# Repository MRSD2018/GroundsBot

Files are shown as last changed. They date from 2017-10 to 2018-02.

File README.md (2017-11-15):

# GroundsBot
A ~~flexible~~ system that can perform regular outdoor grounds maintenance tasks such a ~~sidewalk sweeping~~,
~~snow clearing~~ or grass cutting on extreme terrain for use by grounds care ~~and snow removal~~ companies.

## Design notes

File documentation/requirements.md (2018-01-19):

System Level Requirements

Mandatory Performance Requirements
ID,Requirement,Description

M.P.1, First time user inputs map within 15 minutes, GroundsBot should be easy to use  

M.P.2, System returns proposed route/coverage map within 5 minutes, related to M.P.1 GroundsBot should start up quickly to ease the mind of the user   

M.P.3, Cover 1/4 acre per hour on flat, unobstructed terrain, minimum coverage rate in ideal conditions

M.P.4, Cut 95% of the grass on flat, unobstructed terrain, minimum total coverage in ideal conditions

M.P.5, Navigate 30 degree sloped grass, GroundsBot should be able to handle steep slopes safely

M.P.6 , Detect 80% of static objects greater than 3 inches in height and 2 inches in width, GroundsBot should be able to recognize static obstacles in order to prevent collisions and mowing accidents 

M.P.7 , Detect 80% of dynamic objects greater than 6 inches in height and 6 inches in width travelling less than 4 mph, GroundsBot should be able to recognize obstacles in order to prevent collisions and mowing accidents 

M.P.8 , Mow to within 1 foot of detected obstacles , GroundsBot should be able to detect an obstacle (M.P.6) and navigate around it to continue its mowing path 

M.P.9 , Return home to within 5 feet of starting position , GroundsBot should return to its starting position to remove as much hassle from the user as possible   	  

Desirable Performance Requirements

ID,Requirement,Description

D.P.1 , Mow to within 3 inches of a detected obstacles , A stretch goal for when M.P.8 (mow within 1 ft. of obstacles) is achieved 

D.P.2 , Visually report mowing coverage and obstacles encountered , GroundsBot should report areas it missed to the user so the user knows where to manually mow to achieve full coverage

D.P.3 , Deck adjustable 0.5” to 2” , GroundsBot should be able to meet the grass height standards of different golf courses

Mandatory Non-Functional Requirements
ID,Requirement,Description

M.N.1 , Have a functional and easily accessible emergency stop , GroundsBot should be safe to use and easy to shut down in case of emergency

M.N.2 , Be clearly visible , GroundsBot should indicate its presence and status to everyone nearby 

M.N.3 , Do not tear up grass , GroundsBot should not ruin any area it travels over 

Desirable Non-Functional Requirements

ID,Requirement,Description
D.N.1 , Operates in low light conditions , GroundsBot should operate in low light conditions to avoid interrupting golfers

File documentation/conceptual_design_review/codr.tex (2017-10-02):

\documentclass[12pt]{extarticle}
\usepackage[utf8]{inputenc}
\usepackage{graphicx}
\usepackage{float}
\usepackage{array}
\usepackage{makecell} %line breaks inside table cells
\usepackage{changepage} %temp adjust margins
\usepackage[table]{xcolor} %color tables
\usepackage{outlines}
\usepackage{setspace}
\usepackage{multirow}
\usepackage[export]{adjustbox}% http://ctan.org/pkg/adjustbox
\usepackage{caption}
\usepackage{etoolbox}
\usepackage[margin=1in]{geometry}
\usepackage{tabularx}
\usepackage{titling}
\usepackage{titlesec}
\usepackage{helvet}
\usepackage{indentfirst}
\usepackage{arydshln} %dashed lines (must load in last)

\BeforeBeginEnvironment{tabular}{\fontsize{10}{12}\selectfont}
\AfterEndEnvironment{tabular}{}
\BeforeBeginEnvironment{tabularx}{\fontsize{10}{12}\selectfont}
\AfterEndEnvironment{tabularx}{}

\graphicspath{ {img/} }

\titleformat*{\section}{\bfseries\sffamily\fontsize{14}{16}\selectfont}
\titleformat*{\subsection}{\bfseries\sffamily\fontsize{12}{14}\selectfont}
\titleformat*{\subsubsection}{\bfseries\sffamily\fontsize{12}{14}\selectfont}

\captionsetup[table]{font={small, bf}}
\captionsetup[figure]{font={small, bf}}

\renewcommand{\baselinestretch}{1.1} 

\begin{document}

\definecolor{highlight}{HTML}{9DE6AA} %grudsbo green, light edition
\definecolor{maroon}{cmyk}{0,0.87,0.68,0.32}
\definecolor{badhighlight}{HTML}{FF0000}

\title{GroundsBot: Autonomous Golf Course Maintenance \\[.5ex]
		\Large Conceptual Design Review}
\date{September 2017}
\author{CMU MRSD Team A        \\ Sponsor: Discovery Robotics \\ David Evans \\
        Adam Driscoll \\ Henry Chen  \\
        Josh Bennett  \\ Joe Phaneuf \\ }

\maketitle
\def\svgwidth{\columnwidth}
\input{img/groundsbot_logo.pdf_tex}
\newpage

\begin{spacing}{0.95}
\tableofcontents
\end{spacing}

\newpage

\newpage
\section{Project Description}

People spend a lot of time mowing grass. This is particularly true for golf courses. Golf courses have hundreds of acres of land requiring careful maintenance. The median club in the United States spends \$1.2 million per year on maintenance \cite{clubbenchmarking}. A Pittsburgh area golf course superintendent \cite{interview-duxbury} revealed that his staff spends 65\% of their time mowing, and 60\% of that time is spent just on the rough. This is an industry ripe for automation.
\\

Autonomous mowers are commercially available today, however most of these units require buried wires, beacons, or extensive mapping to provide boundaries. For a golf course, the mowing area is so large that those setup methods are a barrier to deployment. The GroundsBot team aims to deliver an autonomous mower that can be deployed with minimal infrastructure, using a coarse boundary map provided by the user.

\newpage
\section{Use Case}
\begin{table}[H]
  \def\arraystretch{4}
   \setlength\tabcolsep{8pt}

\begin{tabularx}{\textwidth}{cX}
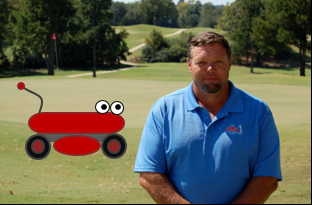
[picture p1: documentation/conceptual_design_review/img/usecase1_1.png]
 & 
Meet Steve. He's a golf course superintendent responsible for keeping the golf course looking professional. Right now, Steve and his groundskeeping team spend 65\% of their time just mowing grass. To save time, Steve just bought a GroundsBot unit to autonomously mow the rough around his golf course. \\
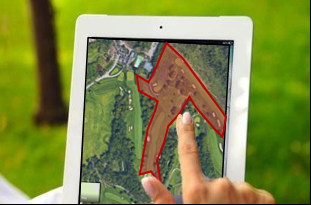
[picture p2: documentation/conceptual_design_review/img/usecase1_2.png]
 &
To start the mowing process, Steve first has to draw an outline of the area he wants mowed. He also highlights any zones Groundsbot should avoid while mowing.
\\
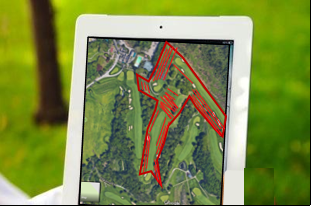
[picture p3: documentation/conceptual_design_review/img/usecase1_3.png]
 &
With the area to mow now outlined, the Groundsbot planning software creates a global route to cover all of the requested area. It avoids large obstacles like fairways, forests, and parking lots.
\\
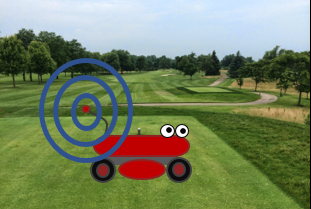
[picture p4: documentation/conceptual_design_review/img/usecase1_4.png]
 &
GroundsBot recieves the global route and localizes through GPS to determine where it is on the golf course.
\\
\end{tabularx}
\end{table}

\begin{table}[H]
   \def\arraystretch{4}
   \setlength\tabcolsep{8pt}

\begin{tabularx}{\textwidth}{cX}
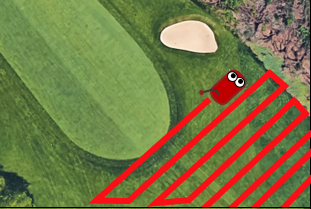
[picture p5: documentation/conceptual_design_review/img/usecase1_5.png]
 &
With the unit located and a global plan uploaded, GroundsBot begins mowing the area specified by Steve. It moves back and forth cutting the grass precisely, matching the quality care provided by Steve and his groundskeeping team.
\\
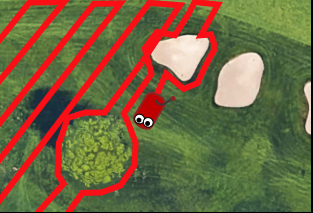
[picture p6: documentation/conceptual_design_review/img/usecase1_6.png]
 &
If GroundsBot encounters unplanned obstacles like sand traps or individual trees, GroundsBot avoids the obstacle and cuts around it. Once GroundsBot has avoided the obstacle in its path, it continues with the original plan.
\\
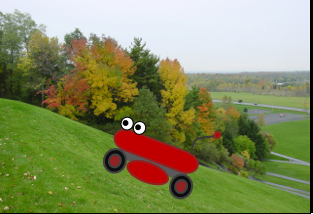
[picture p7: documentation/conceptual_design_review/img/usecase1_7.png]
 &
In order to maximize coverage, GroundsBot will navigate difficult terrain on a golf course, cutting the rough on steep hills.
\\
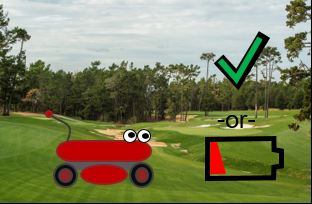
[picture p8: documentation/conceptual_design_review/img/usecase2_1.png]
 &
Once GroundsBot is finished or low on power, it notifies Steve and returns back to the charging dock.
\\

\end{tabularx}
\end{table}

\begin{table}[H]
   \def\arraystretch{4}
   \setlength\tabcolsep{8pt}

\begin{tabularx}{\textwidth}{cX}
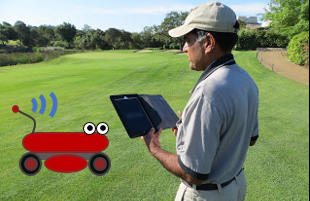
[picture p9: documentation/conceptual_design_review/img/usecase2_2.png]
 &
GroundsBot collected a lot of data while it was out cutting. It transfers diagnostics, coverage reports, and cutting data to Steve’s mobile device.
\\
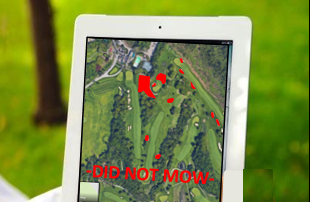
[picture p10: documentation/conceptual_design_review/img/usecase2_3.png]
 &
From here, Steve can analyze what areas of the course GroundsBot missed and what areas he has to send his team out to trim or tidy up.
\\
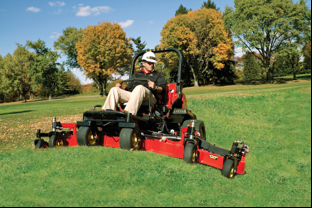
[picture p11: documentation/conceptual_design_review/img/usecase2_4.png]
 &
Steve sends out his groundskeeping team to quickly address missed spots or edging. This is a much faster experience for the team because they only have to touch up a few areas on the course.
\\
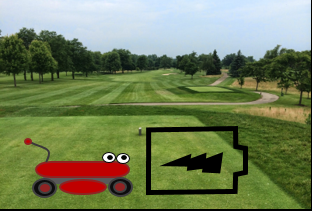
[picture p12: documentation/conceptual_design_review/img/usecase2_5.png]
 &
With the course looking professional, Steve and his groundskeeping team are happy they don’t have to worry about mowing. GroundsBot recharges to prepare for another day of mowing.
\\

\end{tabularx}
\end{table}

\newpage
\section{System Level Requirements}

The system requirements were decided upon to demonstrate a proof of concept autonomous lawn mower that can be set up with minimal added infrastructure. The only added infrastructure will be a docking station for GroundsBot. To accomplish this, GroundsBot must be able to localize with extreme accuracy in an unknown environment. GroundsBot must also be able to navigate consistently along a mowing path plan. Finally, GroundsBot must be able to detect and avoid any obstacles along the way.

\subsection{Mandatory Requirements}
\begin{center}
  \begin{table}[H]
  \caption{Mandatory Performance Requirements}
  \label{table:mandatory performance}

  \def\arraystretch{1.5}
  	\begin{tabularx}{\textwidth}{ lXX }
  	  \hline

		\sffamily\normalsize{ID} & \sffamily\normalsize{Requirement} & \sffamily\normalsize{Description} \\
    	M.P.1 &
    	First time user inputs map within 15 minutes &
    	GroundsBot should be easy to use \\
   		M.P.2 &
   		System returns proposed route/coverage map within 5 minutes &
   		Related to M.P.1, GroundsBot should start up quickly to ease the mind of the user \\
   		M.P.3 &
   		Cut 0-25\% overlap for 95\% of grass &
   		When mowing, GroundsBot should cut in a way that accomplishes full grass coverage while maintaining efficiency by reducing overlap\\
		M.P.4 &
		Mow 50$ft^2$ of 30 degree sloped grass &
		GroundsBot should be able to handle steep slopes to eliminate safety hazards \\
		M.P.5 &
		Detect 80\% of objects greater than 27 cubic inches &
		GroundsBot should be able to recognize obstacles in order to prevent collisions and mowing accidents \\
		M.P.6 &
		Mow to within 1 foot of detected obstacles &
		GroundsBot should be able to detect an obstacle (M.P.5) and navigate around it to continue its mowing path \\
		M.P.7 &
		Mow 90\% of a $\frac{1}{4}$ acre area &
		GroundsBot will encounter obstacles along the way preventing it from 100\% coverage \\
	\end{tabularx}
  \end{table}
\end{center}

\subsection{Desirable Performance Requirements}
\begin{center}
  \begin{table}[H]
  \caption{Desirable Performance Requirements}
  \label{table: desirable performance}

  \def\arraystretch{1.5}
  \begin{tabularx}{\textwidth}{ lXX }
      \hline
	  \sffamily\normalsize{ID} & \sffamily\normalsize{Requirement} & \sffamily\normalsize{Description} \\
	  D.P.1 &
	  Mow to within 3 inches of a detected obstacles &
	  A stretch goal for when M.P.6 (mow within 1 ft. of obstacles) is achieved \\
  	  D.P.2 &
  	  Visually report mowing coverage and obstacles encountered &
  	  GroundsBot should report areas it missed to the user so the user knows where to manually mow to achieve full coverage\\
  \end{tabularx}
  \end{table}
\end{center}

\subsection{Mandatory Non-Functional Requirements}
\begin{center}
  \begin{table}[H]
   \caption{Mandatory Non-Functional Requirements}
    \label{table: mandatory non-functional}

    \def\arraystretch{1.5}
    \begin{tabularx}{\textwidth}{ lXX }
     \hline
  	 \sffamily\normalsize{ID} & \sffamily\normalsize{Requirement} & \sffamily\normalsize{Description} \\
	  M.N.1 &
  	  Return home to within 5 feet of dock &
  	  GroundsBot should return to its starting position to remove as much hassle from the user as possible \\  	  
  	  M.N.2 &
  	  Have a functional and easily accessible emergency stop &
  	  GroundsBot should be safe to use and easy to shut down in case of emergency\\
  	  M.N.3 &
  	  Be clearly visible &
  	  GroundsBot should indicate its presence and status to everyone nearby \\
  	  M.N.4 &
  	  Do not tear up grass &
  	  GroundsBot should not ruin any area it travels over \\
  	\end{tabularx}
  \end{table}
\end{center}

\subsection{Desirable Non-Functional Requirements}
\begin{center}
  \begin{table}[H]
  	\caption{Desirable Non-Functional Requirements}
  	\label{table: desirable non-functional}

  	\def\arraystretch{1.5}
	\begin{tabularx}{\textwidth}{ lXX }
  	\hline
  	  \sffamily\normalsize{ID} & \sffamily\normalsize{Requirement} &
  	  \sffamily\normalsize{Description} \\
  	  D.N.1 &
  	  Operates in variable lighting conditions &
  	  GroundsBot should operate at night to avoid interrupting golfers\\
  	  D.N.2 &
  	  Deck adjustable 0.5” to 2” &
  	  GroundsBot should be able to meet the grass height standards of different golf courses\\
  	  D.N.3 &
  	  Bot is resistant to impacts &
  	  GroundsBot should be unaffected if hit by a golf ball while mowing\\
  	  D.N.4 &
  	  Return home to and mate with charging dock &
  	  A stretch goal if M.N.1 (return to within 5 ft. of dock) is achieved \\
	\end{tabularx}
  \end{table}
\end{center}

\newpage
\section{Functional Architecture}
  There are three subsystems that combine to accomplish the functionality needed for GroundsBot (Figure~\ref{fig:functional}). The User Interface accepts inputs from the groundskeeper, generating detailed mowing regions. The Charging Dock acts as a home point for charging the robot, while also providing a reference signal for correcting localization issues. The Mowing Robot includes internal subsystems which enable the robot to navigate the golf course, cut the rough, and return to the charging dock when needed.\\
  
\begin{figure}[H]
\centering
\def\svgwidth{\columnwidth}
\input{img/functional.pdf_tex}
\caption{Functional Architecture}
\label{fig:functional}
\end{figure}

\newpage
  The Mowing Robot subsystem is responsible for many critical tasks in the Autonomous Golf Rough Mowing system. The Vehicle Platform is one internal subsystem that ensures effective mowing operations by storing energy, providing mobility, and docking when charging is needed. The Mower Electronics subsystem provides electrical controls for the motors and hosts the computing resources needed to run the algorithms for mowing. The sensor data provided by this subsystem is crucial for the remaining systems, enabling full mowing autonomy.\\
  
  The remaining subsystems within the Mowing Robot include Online Perception, Robot Localization, Navigation Planning, and Control. These software systems provide GroundsBot with awareness of surroundings, knowledge of position, and in-depth details about the grass. This enables successful navigation through complicated environments, and provides the information necessary to control GroundsBot effectively.\\

\newpage
\section{System Level Trade Studies}
  \subsection{Platform Configuration Trade Study}
The first step was to decide a platform configuration that will meet the system requirements. A handful of common wheeled platforms \cite{husky} variants were considered (Table \ref{Tab:PlatformConfigDiagramsTable}). Each was evaluated on speed, wheel compaction, stability, complexity, ease of odometry, turning radius, and performance on uneven terrain. A two wheeled chassis with casters was selected (Table \ref{Tab:PlatformConfigTable}).

     \begin{table}[H]

    \caption{Platform Configuration Diagrams}
    \label{Tab:PlatformConfigDiagramsTable}
    \begin{adjustwidth}{-1in}{-1in}
    \centering
    \setlength{\dashlinedash}{.5pt}
    \setlength\tabcolsep{4pt}
    \def\arraystretch{1.2}

    \begin{tabular}{lcccccccc}
    \hline
\makecell{\sffamily\normalsize{Configuration}} & \makecell{\sffamily\normalsize{Description}} & \makecell{\sffamily\normalsize{Diagram}}  \\ 
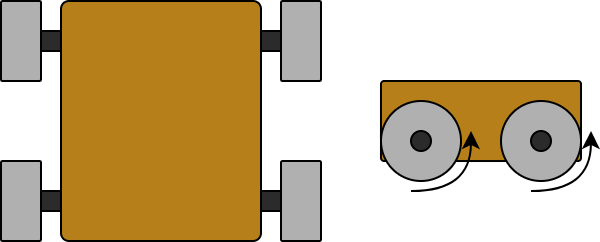
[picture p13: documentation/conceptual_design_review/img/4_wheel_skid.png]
    \makecell[l]{4 Wheel \\ Skid} &  \makecell[l]{Four driven wheels \\ with skid steering.} &  \makecell[l]{\\ } \\  
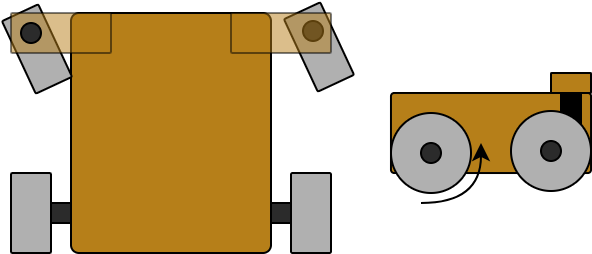
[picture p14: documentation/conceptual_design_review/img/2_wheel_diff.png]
    \makecell[l]{2 Wheel \\ Differential \\ with Casters} &  \makecell[l]{Two driven wheels \\ with casters for free \\ rotation.} &  \makecell[l]{\\ } \\
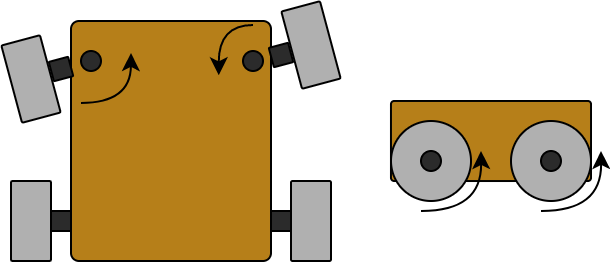
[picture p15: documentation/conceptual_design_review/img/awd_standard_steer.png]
    \makecell[l]{AWD \\ Standard \\ Steering} &  \makecell[l]{Four driven wheels \\ with standard \\differential steering.} &  \makecell[l]{\\ } \\
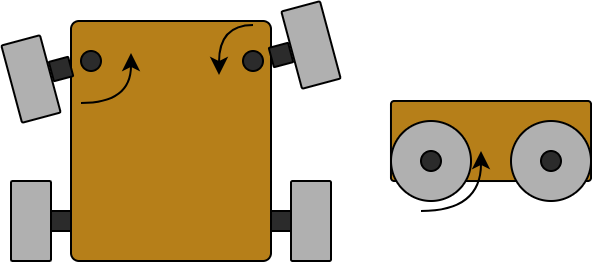
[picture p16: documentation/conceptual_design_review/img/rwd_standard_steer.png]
    \makecell[l]{RWD \\ Standard \\ Steering} &  \makecell[l]{Two driven wheels \\ with standard\\ differential steering.} &  \makecell[l]{\\ } \\
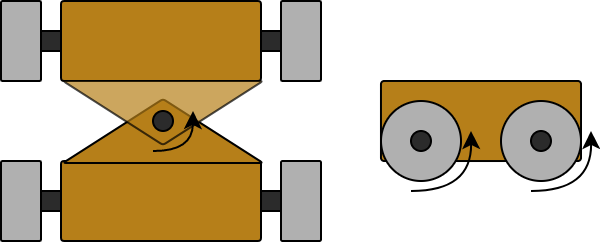
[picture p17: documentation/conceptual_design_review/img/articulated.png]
    \makecell[l]{Articulated} &  \makecell[l]{Four driven wheels \\ with center pivot \\ articulated steering.} &  \makecell[l]{\\ } \\
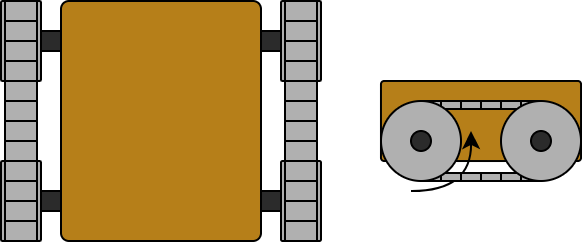
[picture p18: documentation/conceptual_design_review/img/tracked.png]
    \makecell[l]{Tracked} &  \makecell[l]{Two driven wheels \\ with tracks and \\ skid steering.} &  \makecell[l]{\\ } \\
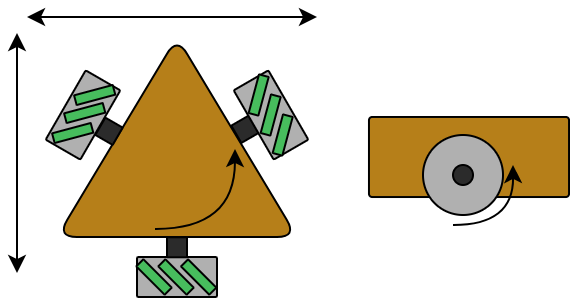
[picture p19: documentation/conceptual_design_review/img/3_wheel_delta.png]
    \makecell[l]{3 Wheel \\ Delta} &  \makecell[l]{Three driven wheels \\ with immediate x, y, \\ and rotation control.} &  \makecell[l]{ } \\
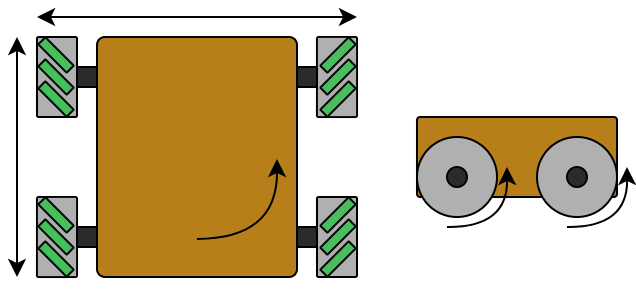
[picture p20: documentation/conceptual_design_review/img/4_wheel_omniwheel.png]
    \makecell[l]{4 Wheel \\ Omniwheel} &  \makecell[l]{Four driven wheels \\ with immediate x, y, \\ and rotation control.} &  \makecell[l]{\\ } \\
    
        \end{tabular}
    
    \end{adjustwidth}
    \end{table}

%%%%%%%%%%%%%%platform config table%%%%%%%%%%%%%%%%%%%%%%%% 
    \begin{table}[H]

    \caption{Platform Configuration Trade Study}
    \label{Tab:PlatformConfigTable}
    \begin{adjustwidth}{-1in}{-1in}
    \centering
    \setlength{\dashlinedash}{.5pt}
    \setlength\tabcolsep{4pt}
    \def\arraystretch{2}

    \begin{tabular}{lcccccccc}
    \hline 
    \\[-5ex]                                                                                      & \makecell{\\ \\ \sffamily\normalsize{Speed}} & \makecell{\\ \sffamily\normalsize{Wheel} \\ \sffamily\normalsize{Compaction}} & \makecell{\\ \\ \sffamily\normalsize{Stability}} & \makecell{\\ \sffamily\normalsize{Platform} \\ \sffamily\normalsize{Complexity}} & \makecell{\\ \sffamily\normalsize{Odometry} \\ \sffamily\normalsize{Accuracy}} & \makecell{\\ \sffamily\normalsize{Turning} \\ \sffamily\normalsize{Radius} } & \makecell{\sffamily\normalsize{Performance} \\ \sffamily\normalsize{on Uneven} \\ \sffamily\normalsize{Terrain}} & \makecell{\\ \\ \sffamily\normalsize{Score}} \\ 
    \makecell[l]{\sffamily Weights \\ (1-5)}                                            & 3     & 2                & 1         & 3                   & 4                 & 5                                          & 5                             &       \\ \hline
    
    \\[-3ex]
    \sffamily\makecell[l]{4 Wheel \\ Skid}                                             & 5     & 4                & 4         & 4                   & 1                 & 1                                          & 5                             & 73    \\ \hdashline 
    
    %jesus christ this row is a goddamn mess BUT YOU GOTTA DO WHAT YOU GOTTA DO
    \cellcolor{highlight}\sffamily\makecell[l]{2 Wheel \\ Differential \\ with Casters}& \multicolumn{1}{c}{\cellcolor{highlight}4} & \multicolumn{1}{c}{\cellcolor{highlight}3} & \multicolumn{1}{c}{\cellcolor{highlight}4} & \multicolumn{1}{c}{\cellcolor{highlight}5} & \multicolumn{1}{c}{\cellcolor{highlight}5} & \multicolumn{1}{c}{\cellcolor{highlight}5} & \multicolumn{1}{c}{\cellcolor{highlight}5} & \multicolumn{1}{c}{\cellcolor{highlight}107}   \\ \hdashline
    
    \sffamily\makecell[l]{AWD \\ Standard \\ Steering}                                 & 5     & 4                & 4         & 2                   & 4                 & 2                                          & 5                             & 84    \\ \hdashline
    \sffamily\makecell[l]{RWD \\ Standard \\ Steering}                                 & 5     & 4                & 4         & 3                   & 5                 & 2                                          & 5                             & 91    \\ \hdashline
    \sffamily\makecell[l]{ \\ Articulated \\ \quad }                                   & 3     & 4                & 2         & 1                   & 3                 & 2                                          & 5                             & 69    \\ \hdashline
    \sffamily\makecell[l]{\\ Tracked  \\ \quad}                                        & 2     & 5                & 5         & 3                   & 1                 & 5                                          & 5                             & 84    \\ \hdashline
   \sffamily\makecell[l]{3 Wheel \\ Delta}                                            & 1     & 3                & 1         & 1                   & 1                 & 5                                          & 1                             & 47    \\ \hdashline
    \sffamily\makecell[l]{4 Wheel \\ Omniwheel}                                        & 2     & 4                & 2         & 1                   & 5                 & 5                                          & 1                             & 69    \\ 
    \end{tabular}
  
    \end{adjustwidth}
    \end{table}
    
%%%%%%%%%%platform base table%%%%%%%%%%%%%%%%%%%%%%%%%%%%   
Once a base configuration was determined, a specific implementation of the platform needed to be chosen. Several off-the-shelf as well as DIY platforms were considered \cite{husqvarna} \cite{superdroid}. A DIY platform was chosen (Table \ref{Tab:PlatformBaseTable}).

    \begin{table}[H]
    \begin{adjustwidth}{-1.5in}{-1.5in}
    \centering
    \setlength{\dashlinedash}{.4pt}
    \setlength\tabcolsep{4pt}
    \def\arraystretch{1.8}
    \caption{Platform Base Trade Study}
    \label{Tab:PlatformBaseTable} 
    
    \vspace{1em}

    \begin{tabular}{lcccccccc}
    \hline
    \\[-5ex]
                                                               & \normalsize\sffamily\makecell{ {Ease} \\ { of }\\  {Integration}} &\normalsize\sffamily\makecell{ {Ease} \\  {of} \\  {Repair}} & \normalsize\sffamily\makecell{ {Ease} \\  {of} \\  {Construction}} & \normalsize\sffamily\makecell{ {Flexibility} \\  {for} \\  {Modifications}} & \normalsize\sffamily\makecell{\\ \\  {Cost}} & \normalsize\sffamily\makecell{ \\  {Lead-} \\  {time}} & \normalsize\sffamily\makecell{\\ \\  {Traction}} & \normalsize\sffamily\makecell{\\ \\  {Score}} \\
    \sffamily Weights (1-5)                                          & 3                   & 2              & 3                    & 5                              & 3    & 2        & 4        &       \\ \hline
    
    \\[-2ex]
    \multicolumn{1}{l}{\sffamily\cellcolor{highlight}Complete DIY}& \multicolumn{1}{c}{\cellcolor{highlight}4} & \multicolumn{1}{c}{\cellcolor{highlight}5} & \multicolumn{1}{c}{\cellcolor{highlight}2} & \multicolumn{1}{c}{\cellcolor{highlight}5} & \multicolumn{1}{c}{\cellcolor{highlight}4} & \multicolumn{1}{c}{\cellcolor{highlight}4} & \multicolumn{1}{c}{\cellcolor{highlight}5} & \multicolumn{1}{c}{\cellcolor{highlight}93}    \\ \hdashline
   \sffamily RC Lawnmower                                           & 5                   & 3              & 5                    & 4                              & 1    & 2        & 5        & 83    \\ \hdashline
    \sffamily\makecell[l]{Modify Robot \\ Lawnmower}                & 3                   & 3              & 4                    & 1                              & 1    & 4        & 2        & 51    \\ \hdashline
    \sffamily\makecell[l]{Modify Electric \\ Push Mower}             & 2                   & 2              & 3                    & 1                              & 2    & 5        & 1        & 44    \\ \hdashline
    \sffamily\makecell[l]{Modify Electric \\ Ride on Mower}         & 2                   & 1              & 3                    & 1                              & 3    & 5        & 5        & 61    \\ \hdashline
    \sffamily\makecell[l]{Stock Platform with \\ Mower Attached}    & 5                   & 3              & 5                    & 4                              & 1    & 3        & 3        & 77    \\ 
    \end{tabular}
    
    \end{adjustwidth}
    \end{table}
    
\subsection{Sensor Trade Study}

%%%%%%%%%%sensor capability table%%%%%%%%%%%%%%%%%%%%   
Once the platform was decided upon, analysis on different sensors and sensor combinations began. Sensors were evaluated individually first to establish baseline capability and relevance to the project. Then sensors were evaluated in different combinations, taking into account the results of the individual sensor study. The results showed that a stereo vision camera was the sensor that best fit the needs of GroundsBot (Table \ref{Tab:SensorCapabilitiesTable}).

    \begin{table}[H]
    \begin{adjustwidth}{-1.5in}{-1.5in}
    \setlength{\dashlinedash}{.4pt}
    \setlength\tabcolsep{4pt}
    \def\arraystretch{1.3}
    \centering

    \caption{Sensor Capabilities}
    \label{Tab:SensorCapabilitiesTable}
    
    \vspace{1em}

    \begin{tabular}{lcccccc}
    \hline
                                                                     & \normalsize\sffamily\makecell{ {Identify} \\  {Static}  \\  {Obstacles}} & \normalsize\sffamily\makecell{ {Identify} \\  {Dynamic} \\  {Obstacles}} & \normalsize\sffamily\makecell{ {Detect} \\  {Grass /} \\  {No Grass}} & \normalsize\sffamily\makecell{ {Functions} \\  {Outdoors} \\  {In Daylight}} & \normalsize\sffamily\makecell{ {Detect} \\  {Grass} \\  {Transitions}} & \normalsize\sffamily\makecell{ {Sense} \\ Driveable \\  {Land}} \\ 
        \hline
    \\[-2ex]
    \sffamily LiDAR                                                        & 5                         & 5                          & 0                       & 5                              & 0                        & 5                    \\ \hdashline
    \sffamily Camera                                                       & 3                         & 3                          & 5                       & 5                              & 5                        & 1                    \\ \hdashline
    
    \multicolumn{1}{l}{\sffamily\cellcolor{badhighlight!70}RGBD Camera }& \multicolumn{1}{c}{\cellcolor{badhighlight!70}5} & \multicolumn{1}{c}{\cellcolor{badhighlight!70}5 } & \multicolumn{1}{c}{\cellcolor{badhighlight!70}5 } & \multicolumn{1}{c}{\cellcolor{badhighlight!70}5 }   & \multicolumn{1}{c}{\cellcolor{badhighlight!70}0 } & \multicolumn{1}{c}{\cellcolor{badhighlight!70}5 } \\ \hdashline
    \sffamily\makecell[l]{Omnidirectional \\ Camera (upwards)}            & 3                         & 3                          & 0                       & 5                              & 0                        & 0                    \\ \hdashline
    \sffamily Stereo Camera                                                & 4                         & 3                          & 5                       & 5                              & 5                        & 3                    \\ \hdashline
    \sffamily Thermal Camera                                               & 1                         & 5                          & 0                       & 5                              & 0                        & 1                    \\ \hdashline
    \sffamily Sonar                                                        & 3                         & 3                          & 0                       & 5                              & 0                        & 2                   \\    
    \end{tabular}

    \end{adjustwidth}
    \end{table}
    
%%%%%%sensor trade study table%%%%%%%%%%%%%%%%%%%%%%%%%%%
    \begin{table}[H]
    \begin{adjustwidth}{0in}{0in}
    \setlength{\dashlinedash}{.4pt}
    \setlength\tabcolsep{4pt}
    \def\arraystretch{1.3}
    \centering
    
    \caption{Perception Sensor Trade Study}
    \label{Tab:PerceptionSensorTable}
    
    \vspace{1em}

    \begin{tabular}{lcccccc}
    \hline
    \\[-2ex]
                                                                     & \normalsize\sffamily\makecell{\\ \\  {Ability}} & \normalsize\sffamily\makecell{\\ \\  {Cost}} & \normalsize\sffamily\makecell{ {Hardware} \\  {Integration} \\  {Complexity}} & \normalsize\sffamily\makecell{ {Software} \\  {Integration} \\  {Complexity}} & \normalsize\sffamily\makecell{ \\  {Computational} \\  {Intensity}} & \normalsize\sffamily\makecell{\\ \\  {Score}} \\ 
    \sffamily Weights                                                      & 5       & 3    & 4                               & 5                               & 3                       &       \\ \hline
    \\[-2ex]
    \sffamily LiDAR + 1x Camera                                            & 4       & 2    & 3                               & 4                               & 3                       & 67    \\ \hdashline
    \sffamily LiDAR + Stereo Camera                                        & 5       & 1    & 3                               & 3                               & 2                       & 61    \\ \hdashline
    \sffamily\makecell[l]{Omnidirectional Camera + \\ Down Camera}        & 2       & 5    & 4                               & 2                               & 3                       & 60    \\ \hdashline
    \multicolumn{1}{l}{\sffamily\cellcolor{highlight}Stereo Camera Only}& \multicolumn{1}{c}{\cellcolor{highlight}3} & \multicolumn{1}{c}{\cellcolor{highlight}4} & \multicolumn{1}{c}{\cellcolor{highlight}5} & \multicolumn{1}{c}{\cellcolor{highlight}4} & \multicolumn{1}{c}{\cellcolor{highlight}4} & \multicolumn{1}{c}{\cellcolor{highlight}79}    \\ \hdashline
    \sffamily\makecell[l]{Thermal Camera + \\ LiDAR + Camera}             & 4.5     & 1    & 3                               & 2                               & 2                       & 53.5  \\ \hdashline
    \sffamily Many Cameras                                                 & 3       & 4    & 2                               & 2                               & 2                       & 51    \\ 
    
    \end{tabular}

    \end{adjustwidth}
    \end{table}

\newpage
\section{Cyberphysical Architecture}
\begin{figure}[H]
\centering
\def\svgwidth{\columnwidth}
\input{img/cyberphysical.pdf_tex}
\caption{Cyberphysical Architecture}
\label{fig:cyberphysical}
\end{figure}

  The user interface and IO subsystems are the contact points for the operator. The WiFi access point allows the user to load mowing boundaries from their laptop or mobile device. This also enables the user to download coverage reports and diagnostics. Status LEDs allow the operator to understand the system status at a glance, while safety beacons alert humans to GroundsBot's presence at a distance.\\

  GroundsBot uses its sensor suite to ensure a clean cut. GPS \cite{swiftnav}, IMU, and Motor Encoders are used for coarse localization while the cameras are used to ensure optimal grass overlap while cutting. Cameras and also enable GroundsBot to detect static and dynamic obstacles. A GPS RTK base station allows for tighter localization.\\

  GroundsBot's battery subsystem reports charge status to the CPU to prevent GroundsBot from becoming stranded. The battery subsystem also contains standard protection protocols including charge control, under-voltage lockout, and over-current protection. \\

  The CPU utilizes sensor information for localization, obstacle detection, and planning. After a local path is devised drive signals are sent to the motors. The CPU also logs coverage data and generates reports.\\

  The Drive Train contains motors and motor drivers to propel GroundsBot across a golf course. This also encompasses the mowing apparatus and mowing deck height control. \\

\newpage
\section{Subsystem Descriptions}
  \subsection{UI}
  It is critical for the user to communicate a desired mowing path to the robot. This input method must be separate from the robot itself, allowing the user to be somewhere else as the robot mows autonomously. \\
  
  This will be achieved through a mobile device, either a dedicated tablet or the user's own smartphone. An app or website will be loaded onto this device and allow for the user to input a map outline that will be communicated to the robot. 
  
  \subsection{Hardware}
    \subsubsection{Platform}
      Based on the trade study, a differential drive system with two drive wheels and caster wheels will be used. Another trade study was used to narrow down the platform to a DIY platform instead of a preexisting platform. This custom platform will utilize aluminum extrusions, allowing for easy re-sizing of the platform as well as simple adjustment of the sensor mounts. Currently, motors and batteries from Discovery Robotics will be integrated, but alternate products may be also be considered. 
      
    \subsubsection{Mower}
      In addition to navigating a plot of grass, the system also needs to mow it. Given that a custom platform will be made, this will be done by attaching an existing electric push mower to the robot platform. Alternatively, it will also be possible to attach the blades from a manual reel mower to the platform. 
  
  \subsection{Software}
    \subsubsection{Planner}
      The planner subsystem consists of two parts: a global planner and a local planner. The global planner will take the user input from the UI and translate the input into a path that the robot will follow. This involves refining the outline that was provided by the user and then finding a path that will allow for maximum coverage of the selected area. \\ 
      
      The local planner will be responsible for adapting the route on-the-fly to avoid any obstacles that the robot may encounter. This system will also drive to and from the dock and cutting area. 
      
    \subsubsection{Localization and Perception}
      An accurate description of the robot global position and orientation will be obtained from this subsystem. This information may be obtained from a high-accuracy GPS system, such as RTK-GPS, but visual SLAM based methods will also be investigated. \\
      
      The vision system will also be used to detect boundaries of the grass as the robot approaches the boundary. For obstacle detection, our trade study determined that a stereo camera system would best fit the detection requirements. However, if needed, a LiDAR may be added to improve the detection accuracy. 
    
    \subsubsection{Mobility}
      The mobility subsystem will be responsible for controlling the robot motors. Part of this involves the robot going from point A to point B at any given time. Using current position information from the localization subsystem, this subsystem will find the next waypoint that will allow for the robot to follow the predetermined plan and then transmit the necessary motor control signals to move towards this waypoint. \\
      
      The cutter motor speeds will also be controlled by this subsystem. This subsystem must both detect the speed of the motor, as well as apply the correct motor signals to maintain a constant speed when the cutter encounters an obstacle. 

\newpage
\section{Project Management}
\subsection{Work Plan}
\subsubsection{Tasks}
The GroundsBot work plan is shown in the list below. The plan is separated into high level categories and underlying subtasks. \\

\begin{itemize}
  \item [] \textbf{Chassis}
    \subitem Complete BOM
    \subitem Design Power Distribution and Sensor Integration PCBs % Changed to PCBs from PCBAs because we are "designing PCBs
    \subitem Design Chassis
    \subitem Design GPS RTK Base Station
    \subitem Acquire Parts
    \subitem Integrate Subsystems
  \item [] \textbf{Simulation}
    \subitem Design Simulation Environment
    \subitem Complete Cursory Simulations
  \item [] \textbf{Localization}
    \subitem Integrate GPS + RTK Localization
  \item [] \textbf{Perception}
    \subitem Develop Static Obstacle Detection
    \subitem Develop Dynamic Obstacle Detection
  \item [] \textbf{Planning}
    \subitem Develop Global Route Planner
    \subitem Develop Obstacle Rerouting
  \item [] \textbf{Control}
    \subitem Develop Motor Control
  \item [] \textbf{UI}
    \subitem Create Web Application for Mapping
\end{itemize}

\subsubsection{Schedule}
The full list of milestones is laid out below in Table \ref{Tab:table_milestones}\\ 

\begin{table}[H]
\def\arraystretch{1}

\caption{Project Milestones}
\label{Tab:table_milestones}

\begin{tabular}{ll}
\hline
\normalsize\sffamily{Deadline} & \normalsize\sffamily{Milestone}                            \\
\\
Progress Review 1 [OCT 17 2017] & Mechanical CAD Complete \\
    &Electrical CAD Complete                     \\
    &BOM Complete                                \\
    &Parts Ordered                               \\
    &ROS Environment Initialized                 \\
                                               \\
Progress Review 2 [OCT 26 2017] & Chassis Assembled with Mowing Apparatus     \\
    &ROS Simulation Environment Complete         \\
    &GPS RTK Base Station Complete               \\
                                              \\ 
Progress Review 3 [NOV 7 2017] 
    &GroundsBot System Integration Complete      \\
    &GPS RTK Integration Complete                \\
    &Control Systems Demo Complete               \\
                                              \\
Progress Review 4 [NOV 21 2017] 
  
    &GroundsBot Accepts GPS Waypoints            \\
    &GroundsBot Follows GPS Waypoints            \\
    &Teleoperation Test Complete                 \\
                                               \\
Fall Validation Experiment [NOV 28 2017] 
 
    &GroundsBot Follows Route From Web App       \\
    &GroundsBot Differentiates Grass From Other Objects \\
                                            \\
                                            
January 2018

    &Global Planning Algorithm Complete          \\
    &Static and Dynamic Obstacle Detection Complete\\
                                               \\
February 2018
  
    &Read User Map Input                        \\
    &GroundsBot Reroutes Around Obstacles       \\
                                              \\
March 2018 
  
    &Full Mapping UI Complete                   \\
    &GroundsBot Autonomously Cuts Lot           \\
                                              \\
April 2018 

    &Final System Tests Complete                \\                                            \\
\end{tabular}

\end{table}

\subsubsection{Progress Reviews}
\noindent
\textbf{Progress Review 1}: The goal for Progress Review 1 is to have all hardware design complete with parts on order. \\
 \textbf{Progress Review 2}: The goal for Progress Review 2 is to have an assembled frame/chassis, a full ROS simulation environment, and a completed GPS + RTK base station.\\

\subsection{System Validation Experiments}
\subsubsection{Fall Validation Experiment}

	The aim of the fall validation experiment is to test individual subsystems. As such many of the systems requirements set for GroundsBot will not be fully met. All tests to be performed have been designed to indicate significant progress towards reaching the system requirements. More specifically the team plans to test the base functionality of the mobility, localization, planning, and perception subsystems of GroundsBot. The details of the test are laid out below.
\\
\begin{center}
\textbf{Test 1:}
\end{center}
 \textbf{Location:} Field by Doherty Apartments \cite{interview-guenther}
\\
\textbf{Equipment:} GroundsBot, GroundsBot dock/RTK base station, laptop
\begin{enumerate}
  \item Power on GroundsBot next to its docking station
  \item Establish connection between GroundsBot and mobile device
  \item Input GPS waypoints following a typical zigzag pattern a groundskeeper might make when mowing a lawn
  \item Send waypoints to GroundsBot
  \item GroundsBot will navigate to each waypoint entered, in the order they were entered
  \item Once the last waypoint is reached, GroundsBot will navigate back to the docking station (Note: the docking station will not be one of the entered waypoints)
\end{enumerate}

\begin{center}
\textbf{Test 2:}
\end{center}
Test 2 has been designed to demonstrate base functionality of the perception subsystem. The team will present a perception algorithm capable of differentiating between grass (i.e. a mowable surface) and non-grass (i.e. a non-mowable surface.) This test will be performed outside of the fall validation experiment and a replay of the test will be displayed during the fall validation experiment.

\newpage
\subsubsection{Spring Validation Experiment}

	The spring validation experiment will be when the team will test the full GroundsBot system to demonstrate that all system requirements have been met. The details of the test are laid out below.
\begin{center}
 \textbf{Test 1: }
\end{center}
 \textbf{Location:} Field by Doherty Apartments \\
 \textbf{Equipment:} GroundsBot, GroundsBot dock/RTK base station, mobile device \\
\begin{enumerate}
  \item Power on GroundsBot next to its docking station
  \item Open UI on mobile interface and establish a connection with GroundsBot
  \item Have a new user (someone not on Team A) use the UI to draw an outline of the area to be mowed on a map including both static obstacles and a non-mowable surface (i.e. concrete)
  \item Use the UI to submit the mowing area to GroundsBot
  \item GroundsBot will develop a coverage plan of the area input by the user
  \item GroundsBot will navigate to the area to be mowed
  \item Once it has reached the edge of the mowing area it will begin mowing
  \item GroundsBot will detect and avoid any obstacles it comes across while mowing and will also only mow where there is grass
  \item Once GroundsBot has mowed the whole area it will return to the docking station
  \item GroundsBot will generate and transmit a coverage report to the UI indicating areas it could not mow
\end{enumerate}

\subsection{Team Member Responsibilities}
\begin{itemize}
  \item [] \textbf{Joe Phaneuf}
    \subitem  Team Lead
    \subitem  Systems Engineer
    \subitem  Project Management
  \item [] \textbf{Henry Chen}
    \subitem  Mechanical Design
    \subitem  Prototyping
    \subitem  Computer Vision
  \item [] \textbf{Josh Bennett}
    \subitem  Electrical Design
    \subitem  Mechanical Design
    \subitem  Instrumentation and Sensors
  \item [] \textbf{Adam Driscoll}
    \subitem  Control Systems
    \subitem  Perception
  \item [] \textbf{David Evans}
    \subitem  Power Distribution
    \subitem  Motion Planning
    \subitem  Localization and Mapping
\end{itemize}

\subsection{Provisional BOM}
A bill of materials is included in Table \ref{Tab:provisional_bom} with potential components and rough pricing information. Batteries and motors will be loaned to us from Discovery Robotics, reducing overall project cost. The batteries and motors shown in the BOM are backup components to be used if the loaned components do not fulfill project requirements.
\begin{table}[H]
\centering
\def\arraystretch{1.1}
\caption{Provisional BOM}
\label{Tab:provisional_bom}
\begin{tabular}{ llccl }
\hline
    \normalsize\sffamily {Manufacturer} & \normalsize\sffamily {Part No.} & \normalsize\sffamily {QTY} & \normalsize\sffamily {Cost} & \normalsize\sffamily {Description}\\
    \\[-.8ex]
    SuperDroid Robots & TD-111-135 & 1 & \$900 & Wheelchair Motors \& Encoders \\
	SuperDroid Robots & TE-240-030 & 1 & \$330 & Motor Controller \\
	SuperDroid Robots & TD-178-000 & 1 & \$150 & 13" Tiller Tires and Mounting \\
	Caster Connection & S-5210-PRB & 1 & \$70 & 10" Pneumatic Swivel Caster \\
	Smart Battery & SB2425 & 1 & \$700 & 24V 25aH Battery \\
    Smart Battery & DP-RS2 & 1 & \$165 & Battery Charger \\
    NVIDIA & Jetson TX2 Dev Kit & 1 & \$560 &  Embedded GPU \\
	ITEM & Extrusion & 1 & \$400 & Extrusions and Joints \\
	McMaster-Carr & Mechanical Components & 1 & \$500 & Misc Fasteners, Bearings \\
	DigiKey & Electrical Components & 1 & \$600 & Misc Connectors, Components \\[.5ex]
	\hline 
	\\[-2ex]
	Total: &&& \$4,375 &\\

\end{tabular}
\end{table}

\subsection{Risk Management}
\begin{table}[H]
\def\arraystretch{1.7}

\begin{tabular}{p{7cm}p{6cm}c}
 {Risk} &  {Management Strategy} &  {Risk Category}\\
\hline 
 \textbf{Too Few Features for Perception:} 
If we cannot consistently detect grass from non-grass features, perception subsystem will not be able to direct platform accurately
&
Install infrastructure such as fiducials to assist system in recognizing objects.
&
Technical\\

 \textbf{Team Falling Behind Due to Work:} 
Team may overestimate capability and overwhelm itself with assignments.
&
Prepare for risk by managing tasks and using buffer weeks. Mitigate effect by delaying milestones or cutting compromising targets.
&
Schedule\\
 \textbf{Localization Poor for Following Edges:} 
If our localization algorithms cannot accurately follow edge of lawn, system will not mow lawn effectively.
&
Prepare by understanding criticality of localization. Mitigate effect by changing scope of mowing problem or adding infrastructure to assist.
&
Technical\\
 \textbf{Injury from Spinning Blade:} 

Our system has a dangerous cutting instrument. It can injure a team member or a bystander.
&
Prepare by making sure team understands the risk of spinning blade. Put warning lights and sounds to alert bystanders when testing.
&
Technical\\

 \textbf{Poor Weather for Validation Experiments:} 
Poor weather on demonstration days would prevent us from system from performing.
&
Team monitors upcoming weather before validation experiments.  Records the validation experiment before hand and replays in the case of inclement weather conditions.
&
Schedule\\

 \textbf{Team Member Has Family Constraints:} 
Any team member could experience a family emergency or responsibility that occupies their time and focus. One specific concern is Josh's wife is pregnant and expecting in December.
&
Mitigate the effect on entire team by spreading work across several team members and communicating consistently with absent team member to keep them in the loop.
&
Personal\\

 \textbf{Platform Devastating Event:} 
Platform could have electrical, thermal, or kinetic event that leads to its destruction.
&
Team designs platform with risk in mind, and manages parts reserve to quickly rebuild platform if necessary.
&
Technical\\

 \textbf{Subsystem Harder Than Expected:} 
Any subsystem could require more work than expected, taking away focus from other subsystems.
&
Team can prepare by focusing on critical subsystems first, and may revise scope related to subsystem if necessary.
&
Technical\\

\textbf{Not Enough Capital for Development:} 
There is a risk our system requires more money than initially allocated.
&
To mitigate the effect of this event, team will maintain strong relationship with sponsor by providing consistent communication of development progress. Team may also reach out to other sponsors or donors.
&
Schedule\\
\end{tabular}
\end{table}

\begingroup
\newpage
\section{References}
\renewcommand{\section}[2]{}% %Suppress bibliography header, doesn't work with toc
\begin{thebibliography}{}
\bibitem{clubbenchmarking} 
http://www.clubbenchmarking.com/blog/golf-course-maintenance-how-much-should-you-spend
\bibitem{husky} 
https://www.clearpathrobotics.com/husky-unmanned-ground-vehicle-robot/
\bibitem{husqvarna} 
http://www.husqvarna.com/us/products/robotic-lawn-mowers/
\bibitem{swiftnav} 
https://www.swiftnav.com/store?category=GNSS+Modules
\bibitem{superdroid} 
https://www.superdroidrobots.com/shop/item.aspx/prebuilt-2wd-66in-lawn-mower-wc-sold/1983/
\bibitem{interview-duxbury} 
Duxbury, Jeff [Bob O’Connor Golf Course Superintendent]. (2017, September 16). Personal interview.
\bibitem{interview-guenther} 
Guenther, Steve [Carnegie Mellon University Director of Facilities Operations]. (2017, September 22). Personal interview.
\end{thebibliography}
\endgroup

\end{document}

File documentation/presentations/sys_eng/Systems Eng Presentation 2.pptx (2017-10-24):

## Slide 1

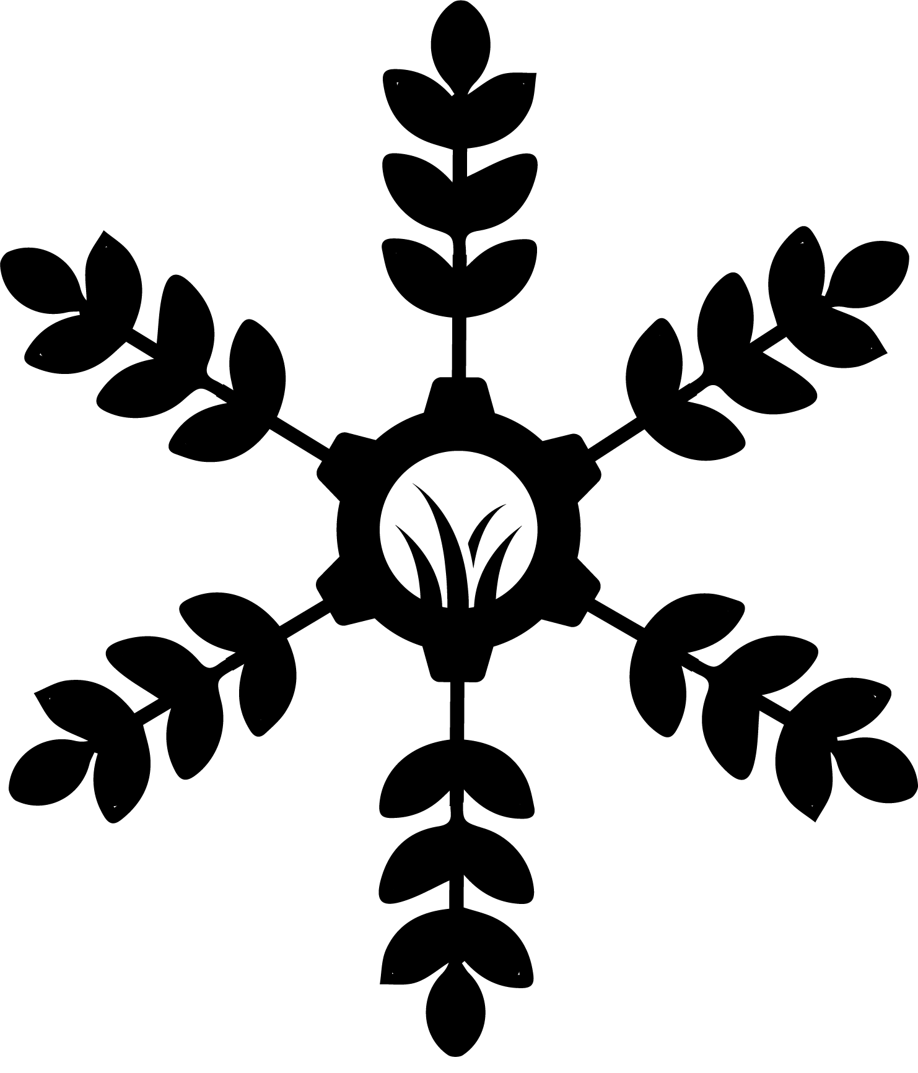
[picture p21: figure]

The A Team:
David Evans
Adam Driscoll
Josh Bennett
Joe Phaneuf
Henry Chen

GROUNDSBOT

The golf course mowing robot

Sponsor:

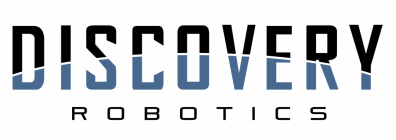
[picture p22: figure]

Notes: Good afternoon!
We are Team A...But you can call us the A-Team
Our team members are David Evans, Adam Driscoll, Henry Chen, Josh Bennett, and myself, Joe Phaneuf
Our gracious and steadfast sponsor is Discovery Robotics
Today we're going to introduce you to the future of autonomous grounds maintenance....
This. Is. GroundsBot!

## Functional Requirements

GroundsBot shall:

ID | Requirement
F.R.1 | Accept boundaries from user
F.R.2 | Cut the rough at desired quality
F.R.3 | Avoid obstacles
F.R.4 | Climb hills
F.R.5 | Return to home

## Performance Requirements

GroundsBot will:

ID | Requirement
M.P.1 | First time user inputs map within 15 minutes
M.P.2 | System returns proposed route/coverage map within 5 minutes
M.P.3 | Cover 1/8 acre in 30 minutes on flat, unobstructed terrain
M.P.4 | Cut 0-25% overlap for 95% of grass
M.P.5 | Navigate 30 degree sloped grass
M.P.6 | Detect 80% of static objects greater than 3 inches in height and 2 inches in width
M.P.7 | Detect 80% of dynamic objects greater than 6 inches in height and 6 inches in width travelling less than 4 mph
M.P.8 | Mow to within 1 foot of detected obstacles
M.P.9 | Return home to within 5 feet of starting position

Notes: Adam
Removed height requirement
Substantially reduced coverage area
Specified object detection rate and static vs dynamic
Removed feedback
M.P.4 – A complicated way of saying we’re going to zig-zag efficiently. If you think about the task of lawn mowing, you want some overlap to ensure you’re not missing any spots. But too much overlap and you’re being inefficient. So these numbers are trying to ensure we don’t miss anything but are still being efficient.

## Non-functional Requirements

GroundsBot will:

ID | Requirement
M.N.1 | Have a functional and easily accessible emergency stop
M.N.2 | Be clearly visible
M.N.3 | Not tear up grass

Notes: Adam
In our first attempt we approached it as GroundsBot the startup company. We’ve realized, while an educational experience, a lot of the NFRs we came up with weren’t relevant within the scope of the school project.
Pretty much all of the old ones are gone and these are the new ones.
Needs to be safe – don’t want to chop off limbs
Needs to be visible for safety as well
Needs to keep the grass in tact.

## Functional Architecture

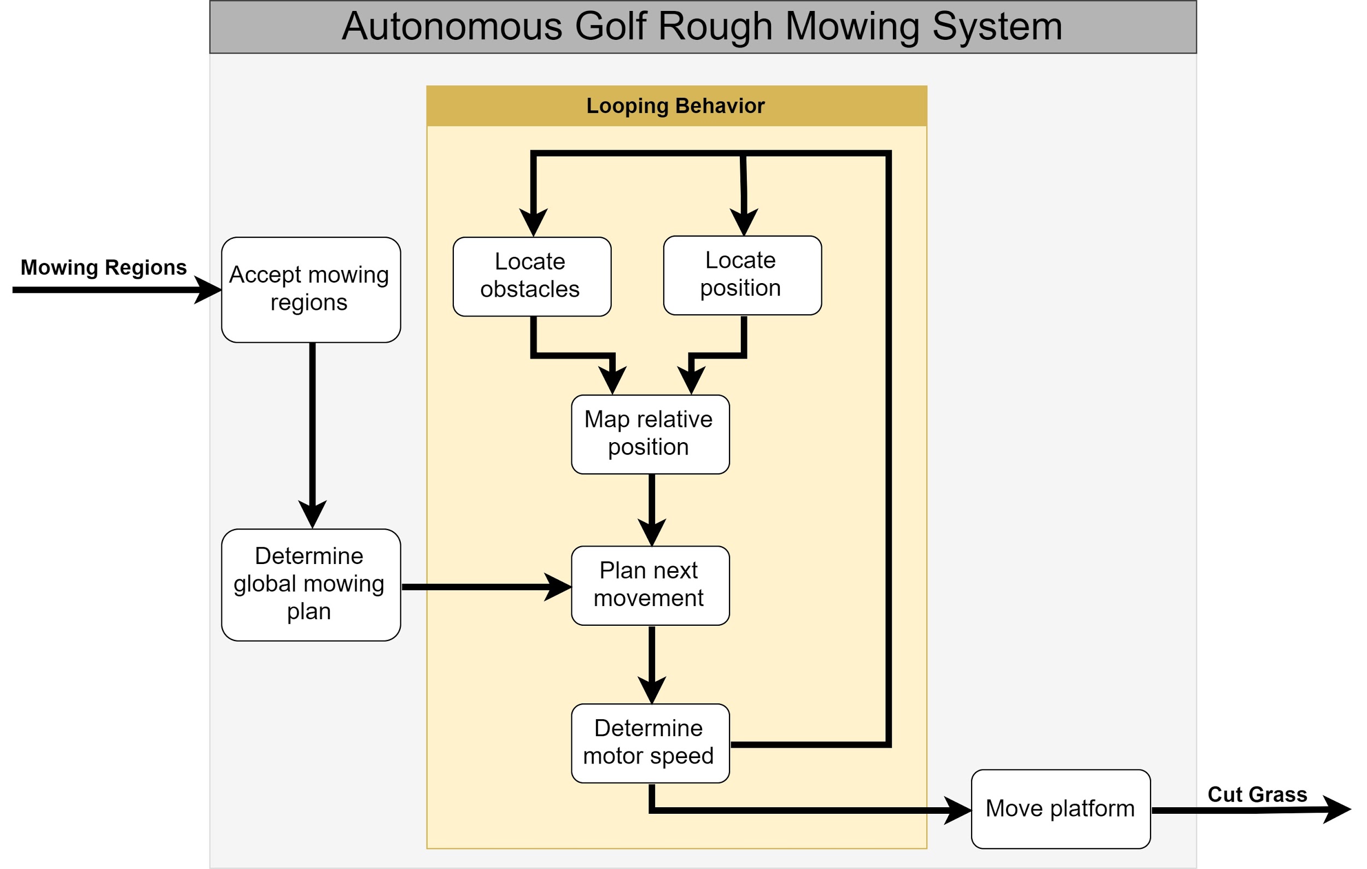
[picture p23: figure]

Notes: Josh

## Cyber-physical Architecture

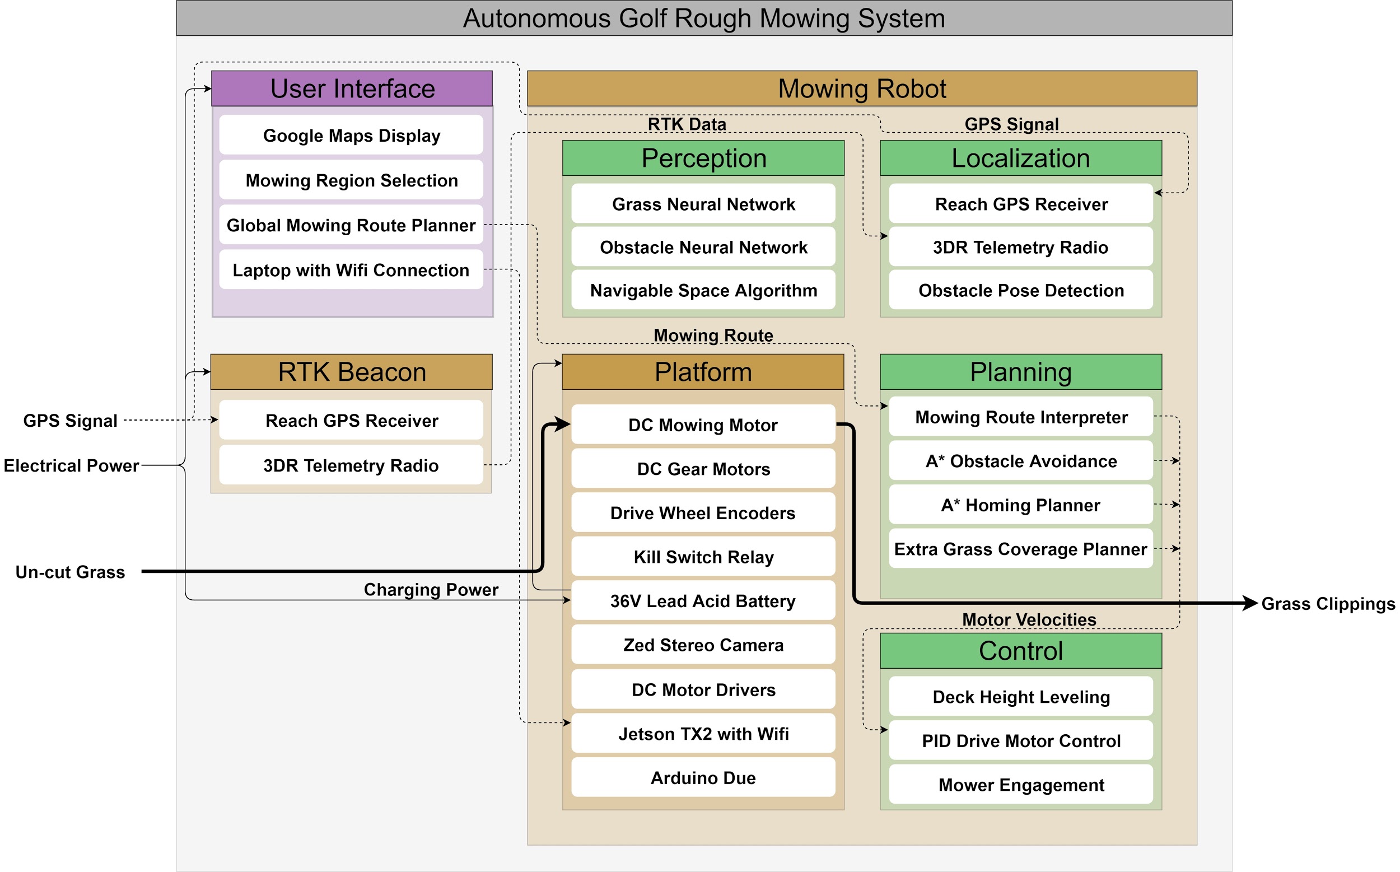
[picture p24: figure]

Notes: Josh

## SVE WBS

UI | Platform | Localization | Perception
App | Electronics | Global localization | Grass (type) detection
| Chassis | Obstacle localization | Static obstacle detection
| Firmware | | Dynamic obstacle detection

Planning | Mapping | Control | Management
Mission Planner | Obstacle mapping | Motor control | Schedule
Local motion Planner | Boundary correction | | Finance
| | | Risk
| | | Personnel

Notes: Joe

## FVE WBS


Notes: Joe

## Schedule


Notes: Joe

## Risks

Risk | Description | Management Strategy | Risk Category
Not Enough Capital for Development: | There is a risk our system requires more money than initially allocated. | Maintain strong relationship with sponsor Reach out to other sponsors or donors Strictly monitor budgeted plan | Schedule
Injury from Spinning Blade: | Our system has a dangerous cutting instrument. It can injure a team member or a bystander. | Make sure team understands risk of testing system Safety tether or switch to shut off mower immediately Put warning lights and sounds to alert bystanders | Technical
Subsystem Harder Than Expected: | Any subsystem could require more work than expected, taking away focus from other subsystems. | Focusing on critical subsystems first, to mitigate failure Revise scope related to subsystem if necessary Budget extra time for extended effort | Technical

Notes: Henry

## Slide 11

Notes: Questions?

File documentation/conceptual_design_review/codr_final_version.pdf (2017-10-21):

# GroundsBot: Autonomous Golf Course Maintenance

## Conceptual Design Review

David Evans Adam Driscoll Henry Chen Josh Bennett Joe Phaneuf; September 2017

CMU MRSD Team A
Sponsor: Discovery Robotics

### Contents

1 Project Description | 3
2 Use Case | 4
3 System Level Requirements | 7
4 Functional Architecture | 9
5 System Level Trade Studies | 11
6 Cyberphysical Architecture | 15
7 Subsystem Descriptions | 16
8 Project Management | 18
9 References | 24

### 1 Project Description

People spend a lot of time mowing grass. This is particularly true for golf courses. Golf courses have hundreds of acres of land requiring careful maintenance. The median club in the United States spends $1.2 million per year on maintenance [1]. A Pittsburgh area golf course superintendent [6] revealed that his staff spends 65% of their time mowing, and 60% of that time is spent just on the rough. This is an industry ripe for automation.

Autonomous mowers are commercially available today, however most of these units require buried wires, beacons, or extensive mapping to provide boundaries. For a golf course, the mowing area is so large that those setup methods are a barrier to deployment. The GroundsBot team aims to deliver an autonomous mower that can be deployed with minimal infrastructure, using a coarse boundary map provided by the user.

### 2 Use Case


Meet Steve. He’s a golf course superintendent responsible for keeping the golf course looking professional. Right now, Steve and his groundskeeping team spend 65% of their time just mowing grass. To save time, Steve just bought a GroundsBot unit to autonomously mow the rough around his golf course.


To start the mowing process, Steve first has to draw an outline of the area he wants mowed. He also highlights any zones Groundsbot should avoid while mowing.


With the area to mow now outlined, the Groundsbot planning software creates a global route to cover all of the requested area. It avoids large obstacles like fairways, forests, and parking lots.


GroundsBot recieves the global route and localizes through GPS to determine where it is on the golf course.


With the unit located and a global plan uploaded, Grounds-Bot begins mowing the area specified by Steve. It moves back and forth cutting the grass precisely, matching the quality care provided by Steve and his groundskeeping team.


If GroundsBot encounters unplanned obstacles like sand traps or individual trees, GroundsBot avoids the obstacle and cuts around it. Once GroundsBot has avoided the obstacle in its path, it continues with the original plan.


In order to maximize coverage, GroundsBot will navigate difficult terrain on a golf course, cutting the rough on steep hills.


Once GroundsBot is finished or low on power, it notifies Steve and returns back to the charging dock.


GroundsBot collected a lot of data while it was out cutting. It transfers diagnostics, coverage reports, and cutting data to Steve’s mobile device.


From here, Steve can analyze what areas of the course GroundsBot missed and what areas he has to send his team out to trim or tidy up.


Steve sends out his groundskeeping team to quickly address missed spots or edging. This is a much faster experience for the team because they only have to touch up a few areas on the course.


With the course looking professional, Steve and his groundskeeping team are happy they don’t have to worry about mowing. GroundsBot recharges to prepare for another day of mowing.

### 3 System Level Requirements

The system requirements were decided upon to demonstrate a proof of concept autonomous lawn mower that can be set up with minimal added infrastructure. The only added infrastructure will be a docking station for GroundsBot. To accomplish this, GroundsBot must be able to localize with extreme accuracy in an unknown environment. GroundsBot must also be able to navigate consistently along a mowing path plan. Finally, GroundsBot must be able to detect and avoid any obstacles along the way.

### 3.1 Mandatory Requirements

Table 1: Mandatory Performance Requirements

ID | Requirement | Description
M.P.1 | First time user inputs map within 15 minutes | GroundsBot should be easy to use
M.P.2 | System returns proposed route/coverage map within 5 minutes | Related to M.P.1, GroundsBot should start up quickly to ease the mind of the user
M.P.3 | Cut 0-25% overlap for 95% of grass | When mowing, GroundsBot should cut in a way that accomplishes full grass coverage while maintaining efficiency by reducing overlap
M.P.4 | Mow 50f t² of 30 degree sloped grass | GroundsBot should be able to handle steep slopes to eliminate safety hazards
M.P.5 | Detect 80% of objects greater than 27 cubic inches | GroundsBot should be able to recognize obsta- cles in order to prevent collisions and mowing accidents
M.P.6 | Mow to within 1 foot of detected obstacles | GroundsBot should be able to detect an obsta- cle (M.P.5) and navigate around it to continue its mowing path
M.P.7 | Mow 90% of a 1
| 4
| acre area | GroundsBot will encounter obstacles along the way preventing it from 100% coverage

### 3.2 Desirable Performance Requirements

Table 2: Desirable Performance Requirements

ID | Requirement | Description
D.P.1 | Mow to within 3 inches of a detected obstacles | A stretch goal for when M.P.6 (mow within 1 ft. of obstacles) is achieved
D.P.2 | Visually report mowing coverage and obstacles encountered | GroundsBot should report areas it missed to the user so the user knows where to manually mow to achieve full coverage

### 3.3 Mandatory Non-Functional Requirements

Table 3: Mandatory Non-Functional Requirements

ID | Requirement | Description
M.N.1 | Return home to within 5 feet of dock | GroundsBot should return to its starting posi- tion to remove as much hassle from the user as possible
M.N.2 | Have a functional and easily accessible emer- gency stop | GroundsBot should be safe to use and easy to shut down in case of emergency
M.N.3 | Be clearly visible | GroundsBot should indicate its presence and status to everyone nearby
M.N.4 | Do not tear up grass | GroundsBot should not ruin any area it travels over

### 3.4 Desirable Non-Functional Requirements

Table 4: Desirable Non-Functional Requirements

ID | Requirement | Description
D.N.1 | Operates in variable lighting conditions | GroundsBot should operate at night to avoid interrupting golfers
D.N.2 | Deck adjustable 0.5” to 2” | GroundsBot should be able to meet the grass height standards of different golf courses
D.N.3 | Bot is resistant to impacts | GroundsBot should be unaffected if hit by a golf ball while mowing
D.N.4 | Return home to and mate with charging dock | A stretch goal if M.N.1 (return to within 5 ft. of dock) is achieved

### 4 Functional Architecture

There are three subsystems that combine to accomplish the functionality needed for GroundsBot (Figure 1). The User Interface accepts inputs from the groundskeeper, generating detailed mowing regions. The Charging Dock acts as a home point for charging the robot, while also providing a reference signal for correcting localization issues. The Mowing Robot includes internal subsystems which enable the robot to navigate the golf course, cut the rough, and return to the charging dock when needed.


Figure 1: Functional Architecture

The Mowing Robot subsystem is responsible for many critical tasks in the Autonomous Golf Rough Mowing system. The Vehicle Platform is one internal subsystem that ensures effective mowing operations by storing energy, providing mobility, and docking when charging is needed. The Mower Electronics subsystem provides electrical controls for the motors and hosts the computing resources needed to run the algorithms for mowing. The sensor data provided by this subsystem is crucial for the remaining systems, enabling full mowing autonomy.

The remaining subsystems within the Mowing Robot include Online Perception, Robot Localization, Navigation Planning, and Control. These software systems provide Grounds-Bot with awareness of surroundings, knowledge of position, and in-depth details about the grass. This enables successful navigation through complicated environments, and provides the information necessary to control GroundsBot effectively.

### 5 System Level Trade Studies

### 5.1 Platform Configuration Trade Study

The first step was to decide a platform configuration that will meet the system requirements. A handful of common wheeled platforms [2] variants were considered (Table 5). Each was evaluated on speed, wheel compaction, stability, complexity, ease of odometry, turning radius, and performance on uneven terrain. A two wheeled chassis with casters was selected (Table 6).

Table 5: Platform Configuration Diagrams

Configuration | Description | Diagram
4 Wheel Skid | Four driven wheels with skid steering.

2 Wheel
Differential
with Casters

Two driven wheels
with casters for free
rotation.

AWD
Standard
Steering

Four driven wheels
with standard
differential steering.

RWD
Standard
Steering

Two driven wheels
with standard
differential steering.

Articulated

Four driven wheels
with center pivot
articulated steering.


Tracked

Two driven wheels
with tracks and
skid steering.

3 Wheel
Delta

Three driven wheels
with immediate x, y,
and rotation control.

4 Wheel
Omniwheel

Four driven wheels
with immediate x, y,
and rotation control.

Table 6: Platform Configuration Trade Study

Speed

Wheel
Compaction Stability

Platform
Complexity

Odometry
Accuracy

Turning
Radius

Performance
on Uneven
| | | | | | | Terrain | Score
Weights
(1-5) | 3 | 2 | 1 | 3 | 4 | 5 | 5

4 Wheel
Skid | 5 | 4 | 4 | 4 | 1 | 1 | 5 | 73

2 Wheel
Differential with Casters | 4 | 3 | 4 | 5 | 5 | 5 | 5 | 107

AWD
Standard Steering | 5 | 4 | 4 | 2 | 4 | 2 | 5 | 84

RWD
Standard Steering | 5 | 4 | 4 | 3 | 5 | 2 | 5 | 91
Articulated | 3 | 4 | 2 | 1 | 3 | 2 | 5 | 69
Tracked | 2 | 5 | 5 | 3 | 1 | 5 | 5 | 84

3 Wheel
Delta | 1 | 3 | 1 | 1 | 1 | 5 | 1 | 47

4 Wheel
Omniwheel | 2 | 4 | 2 | 1 | 5 | 5 | 1 | 69

Once a base configuration was determined, a specific implementation of the platform needed to be chosen. Several off-the-shelf as well as DIY platforms were considered [3] [5]. A DIY platform was chosen (Table 7).

Table 7: Platform Base Trade Study

Ease
of
Integration

Ease
of
Repair

Ease
of
Construction

Flexibility
for
Modifications Cost

Leadtime Traction Score

Weights (1-5) | 3 | 2 | 3 | 5 | 3 | 2 | 4
Complete DIY | 4 | 5 | 2 | 5 | 4 | 4 | 5 | 93
RC Lawnmower | 5 | 3 | 5 | 4 | 1 | 2 | 5 | 83
Modify Robot
Lawnmower | 3 | 3 | 4 | 1 | 1 | 4 | 2 | 51

Modify Electric
Push Mower | 2 | 2 | 3 | 1 | 2 | 5 | 1 | 44

Modify Electric
Ride on Mower | 2 | 1 | 3 | 1 | 3 | 5 | 5 | 61

Stock Platform with
Mower Attached | 5 | 3 | 5 | 4 | 1 | 3 | 3 | 77

### 5.2 Sensor Trade Study

Once the platform was decided upon, analysis on different sensors and sensor combinations began. Sensors were evaluated individually first to establish baseline capability and relevance to the project. Then sensors were evaluated in different combinations, taking into account the results of the individual sensor study. The results showed that a stereo vision camera was the sensor that best fit the needs of GroundsBot (Table 8).

Table 8: Sensor Capabilities

Identify
Static
Obstacles

Identify
Dynamic
Obstacles

Detect
Grass /
No Grass

Functions
Outdoors
In Daylight

Detect
Grass
Transitions

Sense
Driveable
Land
LiDAR | 5 | 5 | 0 | 5 | 0 | 5
Camera | 3 | 3 | 5 | 5 | 5 | 1
RGBD Camera | 5 | 5 | 5 | 5 | 0 | 5
Omnidirectional
Camera (upwards) | 3 | 3 | 0 | 5 | 0 | 0
Stereo Camera | 4 | 3 | 5 | 5 | 5 | 3
Thermal Camera | 1 | 5 | 0 | 5 | 0 | 1
Sonar | 3 | 3 | 0 | 5 | 0 | 2

Table 9: Perception Sensor Trade Study

Ability Cost

Hardware
Integration
Complexity

Software
Integration
Complexity

Computational
| | | | | Intensity | Score
Weights | 5 | 3 | 4 | 5 | 3
LiDAR + 1x Camera | 4 | 2 | 3 | 4 | 3 | 67
LiDAR + Stereo Camera | 5 | 1 | 3 | 3 | 2 | 61
Omnidirectional Camera +
Down Camera | 2 | 5 | 4 | 2 | 3 | 60
Stereo Camera Only | 3 | 4 | 5 | 4 | 4 | 79
Thermal Camera +
LiDAR + Camera | 4.5 | 1 | 3 | 2 | 2 | 53.5
Many Cameras | 3 | 4 | 2 | 2 | 2 | 51

### 6 Cyberphysical Architecture


Figure 2: Cyberphysical Architecture

The user interface and IO subsystems are the contact points for the operator. The WiFi access point allows the user to load mowing boundaries from their laptop or mobile device. This also enables the user to download coverage reports and diagnostics. Status LEDs allow the operator to understand the system status at a glance, while safety beacons alert humans to GroundsBot’s presence at a distance.

GroundsBot uses its sensor suite to ensure a clean cut. GPS [4], IMU, and Motor Encoders are used for coarse localization while the cameras are used to ensure optimal grass overlap while cutting. Cameras and also enable GroundsBot to detect static and dynamic obstacles. A GPS RTK base station allows for tighter localization.

GroundsBot’s battery subsystem reports charge status to the CPU to prevent Grounds-Bot from becoming stranded. The battery subsystem also contains standard protection protocols including charge control, under-voltage lockout, and over-current protection.

The CPU utilizes sensor information for localization, obstacle detection, and planning. After a local path is devised drive signals are sent to the motors. The CPU also logs coverage data and generates reports.

The Drive Train contains motors and motor drivers to propel GroundsBot across a golf course. This also encompasses the mowing apparatus and mowing deck height control.

### 7 Subsystem Descriptions

### 7.1 UI

It is critical for the user to communicate a desired mowing path to the robot. This input method must be separate from the robot itself, allowing the user to be somewhere else as the robot mows autonomously.

This will be achieved through a mobile device, either a dedicated tablet or the user’s own smartphone. An app or website will be loaded onto this device and allow for the user to input a map outline that will be communicated to the robot.

### 7.2 Hardware

### 7.2.1 Platform

Based on the trade study, a differential drive system with two drive wheels and caster wheels will be used. Another trade study was used to narrow down the platform to a DIY platform instead of a preexisting platform. This custom platform will utilize aluminum extrusions, allowing for easy re-sizing of the platform as well as simple adjustment of the sensor mounts. Currently, motors and batteries from Discovery Robotics will be integrated, but alternate products may be also be considered.

### 7.2.2 Mower

In addition to navigating a plot of grass, the system also needs to mow it. Given that a custom platform will be made, this will be done by attaching an existing electric push mower to the robot platform. Alternatively, it will also be possible to attach the blades from a manual reel mower to the platform.

### 7.3 Software

### 7.3.1 Planner

The planner subsystem consists of two parts: a global planner and a local planner. The global planner will take the user input from the UI and translate the input into a path that the robot will follow. This involves refining the outline that was provided by the user and then finding a path that will allow for maximum coverage of the selected area.

The local planner will be responsible for adapting the route on-the-fly to avoid any obstacles that the robot may encounter. This system will also drive to and from the dock and cutting area.

### 7.3.2 Localization and Perception

An accurate description of the robot global position and orientation will be obtained from this subsystem. This information may be obtained from a high-accuracy GPS system, such as RTK-GPS, but visual SLAM based methods will also be investigated.

The vision system will also be used to detect boundaries of the grass as the robot approaches the boundary. For obstacle detection, our trade study determined that a stereo camera system would best fit the detection requirements. However, if needed, a LiDAR may be added to improve the detection accuracy.

### 7.3.3 Mobility

The mobility subsystem will be responsible for controlling the robot motors. Part of this involves the robot going from point A to point B at any given time. Using current position information from the localization subsystem, this subsystem will find the next waypoint that will allow for the robot to follow the predetermined plan and then transmit the necessary motor control signals to move towards this waypoint.

The cutter motor speeds will also be controlled by this subsystem. This subsystem must both detect the speed of the motor, as well as apply the correct motor signals to maintain a constant speed when the cutter encounters an obstacle.

### 8 Project Management

### 8.1 Work Plan

### 8.1.1 Tasks

The GroundsBot work plan is shown in the list below. The plan is separated into high level categories and underlying subtasks.

Chassis

Complete BOM

Design Power Distribution and Sensor Integration PCBs

Design Chassis

Design GPS RTK Base Station

Acquire Parts

Integrate Subsystems

Simulation

Design Simulation Environment

Complete Cursory Simulations

Localization

Integrate GPS + RTK Localization

Perception

Develop Static Obstacle Detection

Develop Dynamic Obstacle Detection

Planning

Develop Global Route Planner

Develop Obstacle Rerouting

Control

Develop Motor Control

UI

Create Web Application for Mapping

### 8.1.2 Schedule

The full list of milestones is laid out below in Table 10

Table 10: Project Milestones

Deadline | Milestone
Progress Review 1 [OCT 17 2017] | Mechanical CAD Complete Electrical CAD Complete BOM Complete Parts Ordered ROS Environment Initialized
Progress Review 2 [OCT 26 2017] | Chassis Assembled with Mowing Apparatus ROS Simulation Environment Complete GPS RTK Base Station Complete
Progress Review 3 [NOV 7 2017] | GroundsBot System Integration Complete GPS RTK Integration Complete Control Systems Demo Complete
Progress Review 4 [NOV 21 2017] | GroundsBot Accepts GPS Waypoints GroundsBot Follows GPS Waypoints Teleoperation Test Complete
Fall Validation Experiment [NOV 28 2017] | GroundsBot Follows Route From Web App GroundsBot Differentiates Grass From Other Objects
January 2018 | Global Planning Algorithm Complete Static and Dynamic Obstacle Detection Complete
February 2018 | Read User Map Input GroundsBot Reroutes Around Obstacles
March 2018 | Full Mapping UI Complete GroundsBot Autonomously Cuts Lot
April 2018 | Final System Tests Complete

### 8.1.3 Progress Reviews

Progress Review 1: The goal for Progress Review 1 is to have all hardware design complete with parts on order.
Progress Review 2: The goal for Progress Review 2 is to have an assembled frame/chassis, a full ROS simulation environment, and a completed GPS + RTK base station.

### 8.2 System Validation Experiments

### 8.2.1 Fall Validation Experiment

The aim of the fall validation experiment is to test individual subsystems. As such many of the systems requirements set for GroundsBot will not be fully met. All tests to be performed have been designed to indicate significant progress towards reaching the system requirements. More specifically the team plans to test the base functionality of the mobility, localization, planning, and perception subsystems of GroundsBot. The details of the test are laid out below.

Test 1:

Location: Field by Doherty Apartments [7]
Equipment: GroundsBot, GroundsBot dock/RTK base station, laptop
1. Power on GroundsBot next to its docking station
2. Establish connection between GroundsBot and mobile device
3. Input GPS waypoints following a typical zigzag pattern a groundskeeper might make when mowing a lawn
4. Send waypoints to GroundsBot
5. GroundsBot will navigate to each waypoint entered, in the order they were entered
6. Once the last waypoint is reached, GroundsBot will navigate back to the docking station (Note: the docking station will not be one of the entered waypoints)

Test 2:

Test 2 has been designed to demonstrate base functionality of the perception subsystem. The team will present a perception algorithm capable of differentiating between grass (i.e. a mowable surface) and non-grass (i.e. a non-mowable surface.) This test will be performed outside of the fall validation experiment and a replay of the test will be displayed during the fall validation experiment.

### 8.2.2 Spring Validation Experiment

The spring validation experiment will be when the team will test the full GroundsBot system to demonstrate that all system requirements have been met. The details of the test are laid out below.

Test 1:

Location: Field by Doherty Apartments
Equipment: GroundsBot, GroundsBot dock/RTK base station, mobile device
1. Power on GroundsBot next to its docking station
2. Open UI on mobile interface and establish a connection with GroundsBot
3. Have a new user (someone not on Team A) use the UI to draw an outline of the area to be mowed on a map including both static obstacles and a non-mowable surface (i.e. concrete)
4. Use the UI to submit the mowing area to GroundsBot
5. GroundsBot will develop a coverage plan of the area input by the user
6. GroundsBot will navigate to the area to be mowed
7. Once it has reached the edge of the mowing area it will begin mowing
8. GroundsBot will detect and avoid any obstacles it comes across while mowing and will also only mow where there is grass
9. Once GroundsBot has mowed the whole area it will return to the docking station
10. GroundsBot will generate and transmit a coverage report to the UI indicating areas it could not mow

### 8.3 Team Member Responsibilities

Joe Phaneuf

Team Lead

Systems Engineer

Project Management

Henry Chen

Mechanical Design

Prototyping

Computer Vision

Josh Bennett

Electrical Design

Mechanical Design

Instrumentation and Sensors

Adam Driscoll

Control Systems

Perception

David Evans

Power Distribution

Motion Planning

Localization and Mapping

### 8.4 Provisional BOM

A bill of materials is included in Table 11 with potential components and rough pricing information. Batteries and motors will be loaned to us from Discovery Robotics, reducing overall project cost. The batteries and motors shown in the BOM are backup components to be used if the loaned components do not fulfill project requirements.

Table 11: Provisional BOM

Manufacturer | Part No. | QTY Cost | Description
SuperDroid Robots | TD-111-135 | 1 | $900 | Wheelchair Motors & Encoders
SuperDroid Robots | TE-240-030 | 1 | $330 | Motor Controller
SuperDroid Robots | TD-178-000 | 1 | $150 | 13” Tiller Tires and Mounting
Caster Connection | S-5210-PRB | 1 | $70 | 10” Pneumatic Swivel Caster
Smart Battery | SB2425 | 1 | $700 | 24V 25aH Battery
Smart Battery | DP-RS2 | 1 | $165 | Battery Charger
NVIDIA | Jetson TX2 Dev Kit | 1 | $560 | Embedded GPU
ITEM | Extrusion | 1 | $400 | Extrusions and Joints
McMaster-Carr | Mechanical Components | 1 | $500 | Misc Fasteners, Bearings
DigiKey | Electrical Components | 1 | $600 | Misc Connectors, Components
Total: | | | $4,375

### 8.5 Risk Management

Risk | Management Strategy | Risk Category
Too Few Features for Perception: If we cannot consistently detect grass from non- grass features, perception subsystem will not be able to direct platform accurately | Install infrastructure such as fiducials to assist system in recognizing objects. | Technical

Team Falling Behind Due to Work: Team may overestimate capability and overwhelm itself with assignments.

Prepare for risk by managing tasks and using buffer weeks. Mitigate effect by delaying milestones or cutting compromising targets.

Schedule

Localization Poor for Following Edges: If our localization algorithms cannot accurately follow edge of lawn, system will not mow lawn effectively.

Prepare by understanding criticality of localization. Mitigate effect by changing scope of mowing problem or adding infrastructure to assist.

Technical

Injury from Spinning Blade:
Our system has a dangerous cutting instrument. It can injure a team member or a bystander.

Prepare by making sure team understands the risk of spinning blade. Put warning lights and sounds to alert bystanders when testing.

Technical

Poor Weather for Validation Experiments: Poor weather on demonstration days would prevent us from system from performing.

Team monitors upcoming weather before validation experiments. Records the validation experiment before hand and replays in the case of inclement weather conditions.

Schedule

Team Member Has Family Constraints: Any team member could experience a family emergency or responsibility that occupies their time and focus. One specific concern is Josh’s wife is pregnant and expecting in December.

Mitigate the effect on entire team by spreading work across several team members and communicating consistently with absent team member to keep them in the loop.

Personal

Platform Devastating Event: Platform could have electrical, thermal, or kinetic event that leads to its destruction.

Team designs platform with risk in mind, and manages parts reserve to quickly rebuild platform if necessary.

Technical

Subsystem Harder Than Expected: Any subsystem could require more work than expected, taking away focus from other subsystems.

Team can prepare by focusing on critical subsystems first, and may revise scope related to subsystem if necessary.

Technical

Not Enough Capital for Development: There is a risk our system requires more money than initially allocated.

To mitigate the effect of this event, team will maintain strong relationship with sponsor by providing consistent communication of development progress. Team may also reach out to other sponsors or donors.

Schedule

### 9 References

[1] http://www.clubbenchmarking.com/blog/golf-course-maintenance-how-much-shouldyou-spend
[2] https://www.clearpathrobotics.com/husky-unmanned-ground-vehicle-robot/
[3] http://www.husqvarna.com/us/products/robotic-lawn-mowers/
[4] https://www.swiftnav.com/store?category=GNSS+Modules
[5] https://www.superdroidrobots.com/shop/item.aspx/prebuilt-2wd-66in-lawn-mower-wcsold/1983/
[6] Duxbury, Jeff [Bob O’Connor Golf Course Superintendent]. (2017, September 16). Personal interview.
[7] Guenther, Steve [Carnegie Mellon University Director of Facilities Operations]. (2017, September 22). Personal interview.

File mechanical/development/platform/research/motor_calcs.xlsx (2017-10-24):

bold = input value | Metric | (units) | Imperial | (unitS)
Approximate Radius: | 0.127 | meters | 5 | inches | 10 | inches diameter wheel
Max Speed: | 6.43736 | kmh | 4 | mph
Required Motor Speed: | 14.08 | rad/s | 2.240901599 | rot/sec
 |  |  | 134.4540959 | RPM
Required Grade: |  |  | 10 | degrees
Acceleration on Grade: | 0.981 | m/s^2 | 0.1 | g's
Approximate Mass: | 54.43104 | kgs | 120 | lbs
Approximate Acceleration Force: | 146.1195076 | Newtons | 32.84898039 | lbf
Approximate Torque: | 9.278588733 | N*m | 82.12245097 | lbf-in
 | 94.64160508 | kgf*cm | 1313.959215 | oz-in
Motor Power: | 130.6425294 | Watts
Actual Motor Power: | 160 | Watts
Actual Motor Speed: | 120 | 100 | 80 | 60 | RPM
Actual Motor Torque: | 12.73 | 15.28 | 19.1 | 25.46 | Nm
Sideways on 30 degree slope:
Mass: | 50 | kg
Angle: | 30
force on 30 degree grade | 245.25 | N
wheel base distance | 0.568
weight distance | 0.13
Sum Moments about wheel origin: | 56.13116197 | N
Required Torque | 7.12865757 | Nm

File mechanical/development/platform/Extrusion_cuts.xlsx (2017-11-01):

Cuts:
1010 | qty | MACHINE
5.5 in | 1 | TOP_1_3_BOTTOM_2
5.5 in | 1 | TOP_1_3_BOTTOM_4
5.083 in | 1 | TOP_1_3_BOTTOM_2_4
2.0 in | 1 | TOP_M6-TAP-CENTER_BOTTOM_1_3
4.265 in | 2 | NONE
3.0 in | 2 | TOP_1
1020 | qty | MACHINE
13.5 in | 2 | TOP_1_4_BOTTOM_1_4 | 1 and 4 are the top and bottom on the 1 inch portion, 2,3 and 5,6 are the side 2 inch portions
13.5 in | 2 | TOP_2_3_BOTTOM_2_3
45.5 in | 2 | TOP_1_4_BOTTOM_1_4
1050 | qty | MACHINE
7.874 in | 4 | NONE
15.5 in | 1 | NONE
4.0 in | 1 | NONE
1012 | qty | MACHINE
2 in | 4 | NONE

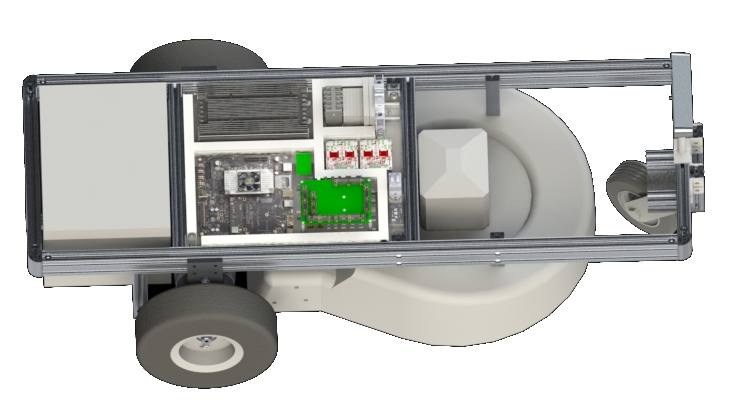
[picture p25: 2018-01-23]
mechanical/development/platform/render/GrudsbyTop.jpg

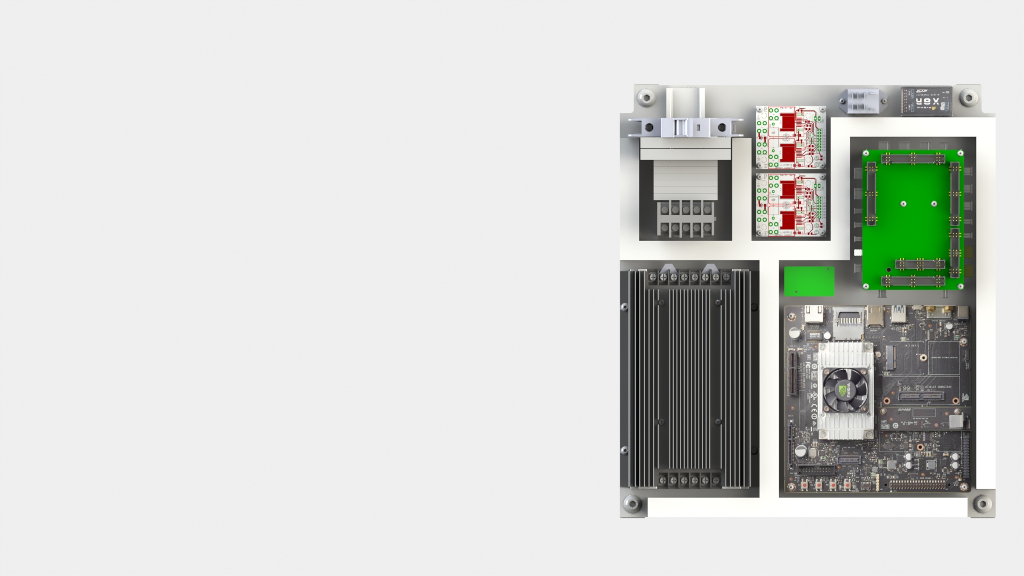
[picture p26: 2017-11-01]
mechanical/development/platform/render/Top View Electrical Panel.JPG

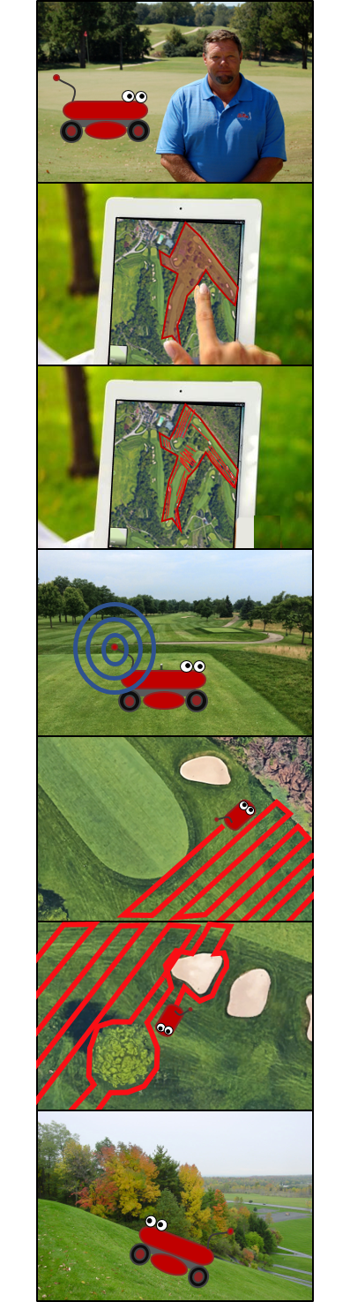
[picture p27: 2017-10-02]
documentation/conceptual_design_review/img/useCasePic1.png

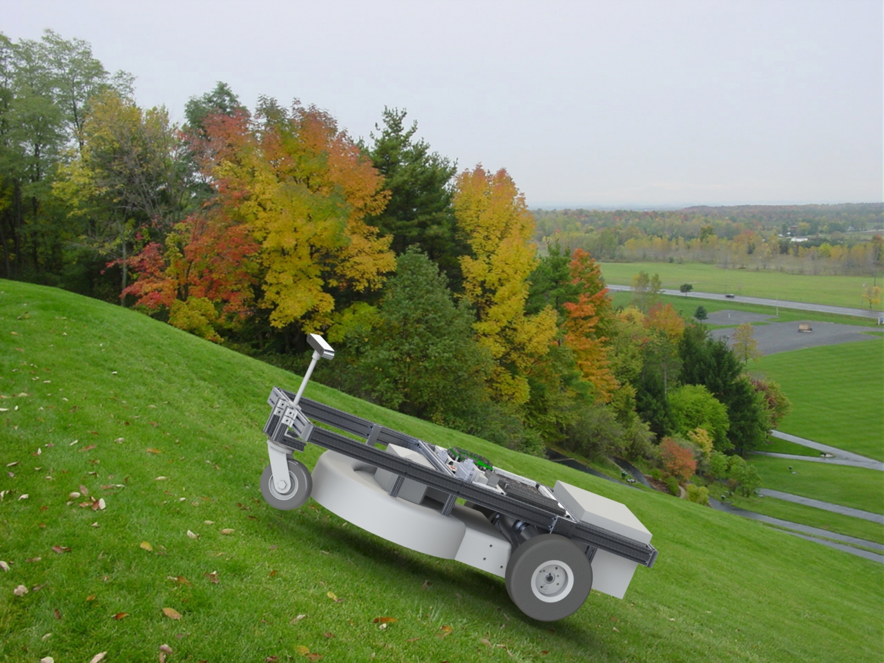
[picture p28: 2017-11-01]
mechanical/development/platform/render/hill.JPG

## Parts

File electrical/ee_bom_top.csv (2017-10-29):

Manufacturer | Manufacturer Part Number | Description | Quantity | Cost | URL
Emlid | REACH RTK KIT | GPS RTK Kit | 1 | 570 | https://emlid.com/shop/reach-rtk-kit/
Stereo Labs | Zed Camera | Stereo Camera USB | 1 | 449 | https://zedstore.stereolabs.com/products/zed
LittelFuse | HLJC1002G | FUSE HLDR 58V 60A INLINE | 1 | 11.9 | https://www.digikey.com/product-detail/en/littelfuse-inc/HLJC1002G/F6111-ND/3427049
LittelFuse | 0895050.U | FUSE AUTOMOTIVE 50A 58V | 1 | 1.94 | https://www.digikey.com/product-detail/en/littelfuse-inc/0895050.U/F4348-ND/3305710
LittelFuse | 0326025.HXP | FUSE 25A 125VDC SLOW | 1 | 1.81 | https://www.digikey.com/product-detail/en/littelfuse-inc/0326025.HXP/F2653-ND/777369
LittelFuse | 01220083Z | FUSE HOLDER 25A |  | 0.71 | https://www.digikey.com/product-detail/en/littelfuse-inc/01220083Z/F3782-ND/2498890
LittelFuse | 0477016.MXP | FUSE 16A 400VDC 5X20mm | 1 | 2.13 | https://www.digikey.com/product-detail/en/littelfuse-inc/0477016.MXP/F2995-ND/1979197
LittelFuse | 0477005.MXP | FUSE 5A 400VDC 5X20 | 1 | 1.70 | https://www.digikey.com/product-detail/en/littelfuse-inc/0477005.MXP/F2990-ND/1979192
Phoenix Contact | 1967375 | Pluggable Terminal Blocks 2 Pos 10.16mm pitch Plug 18-6 AWG Screw | 1 | x | x
Phoenix Contact | 1996236 | Pluggable Terminal Blocks 2 Pos 10.16mm pitch Through Hole Header | 1 | x | x
Phoenix Contact | 1777723 | Pluggable Terminal Blocks 2 Pos 7.62mm pitch Plug 24-8 AWG Screw | 1 | x | x
Phoenix Contact | 1720686 | Pluggable Terminal Blocks 2 Pos 7.62mm pitch Through Hole Header | 1 | x | x
LittelFuse | 0154003.DR | FUSE 3A 125V 9.73x5.03mm | 2 | 1.65 | x | x

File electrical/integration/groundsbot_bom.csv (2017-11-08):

Part | MANUFACTURER | MPN | DESCRIPTION
JETSON1:JETSON_J17_UART1:JP3 | Wurth | 61300611121 | CONN HEADER 6 POS 2.54
JETSON1:JETSON_TX2_J21_EXPANSION1:LED1 | Chicago Miniature Lighting | CMD17-21VGD/TR8 | Led, Green, 1.25mm x 1.4mm, 7mcd, 570nm, Full Reel
JETSON1:JETSON_TX2_J21_EXPANSION1:LED2 | Chicago Miniature Lighting | CMD17-21VGD/TR8 | Led, Green, 1.25mm x 1.4mm, 7mcd, 570nm, Full Reel
JETSON1:JETSON_TX2_J21_EXPANSION1:LED3 | Chicago Miniature Lighting | CMD17-21VGD/TR8 | Led, Green, 1.25mm x 1.4mm, 7mcd, 570nm, Full Reel
JETSON1:JETSON_TX2_J21_EXPANSION1:LED4 | Chicago Miniature Lighting | CMD17-21VGD/TR8 | Led, Green, 1.25mm x 1.4mm, 7mcd, 570nm, Full Reel
JETSON1:JETSON_TX2_J21_EXPANSION1:LED5 | Chicago Miniature Lighting | CMD17-21VGD/TR8 | Led, Green, 1.25mm x 1.4mm, 7mcd, 570nm, Full Reel
JETSON1:JETSON_TX2_J21_EXPANSION1:LED6 | Chicago Miniature Lighting | CMD17-21VGD/TR8 | Led, Green, 1.25mm x 1.4mm, 7mcd, 570nm, Full Reel
JETSON1:JETSON_TX2_J21_EXPANSION1:LED7 | Chicago Miniature Lighting | CMD17-21VGD/TR8 | Led, Green, 1.25mm x 1.4mm, 7mcd, 570nm, Full Reel
JETSON1:JETSON_TX2_J21_EXPANSION1:LED8 | Chicago Miniature Lighting | CMD17-21VGD/TR8 | Led, Green, 1.25mm x 1.4mm, 7mcd, 570nm, Full Reel
JETSON1:JETSON_TX2_J21_EXPANSION1:R1 | Yageo | RC0603FR-0760R4L | RES SMD 60.4 OHM 1% 1/10W 0603
JETSON1:JETSON_TX2_J21_EXPANSION1:R2 | Yageo | RC0603FR-0760R4L | RES SMD 60.4 OHM 1% 1/10W 0603
JETSON1:JETSON_TX2_J21_EXPANSION1:R3 | Yageo | RC0603FR-0760R4L | RES SMD 60.4 OHM 1% 1/10W 0603
JETSON1:JETSON_TX2_J21_EXPANSION1:R4 | Yageo | RC0603FR-0760R4L | RES SMD 60.4 OHM 1% 1/10W 0603
JETSON1:JETSON_TX2_J21_EXPANSION1:R5 | Yageo | RC0603FR-0760R4L | RES SMD 60.4 OHM 1% 1/10W 0603
JETSON1:JETSON_TX2_J21_EXPANSION1:R6 | Yageo | RC0603FR-0760R4L | RES SMD 60.4 OHM 1% 1/10W 0603
JETSON1:JETSON_TX2_J21_EXPANSION1:R7 | Yageo | RC0603FR-0760R4L | RES SMD 60.4 OHM 1% 1/10W 0603
JETSON1:JETSON_TX2_J21_EXPANSION1:R8 | Yageo | RC0603FR-0760R4L | RES SMD 60.4 OHM 1% 1/10W 0603
JETSON1:JETSON_TX2_J21_EXPANSION1:R9 | Yageo | RC0603FR-0710KL | RES SMD 10K OHM 1% 1/10W 0603
JETSON1:JETSON_TX2_J21_EXPANSION1:R10 | Yageo | RC0603FR-0710KL | RES SMD 10K OHM 1% 1/10W 0603
JETSON1:JETSON_TX2_J21_EXPANSION1:U$3 | 3M | N2530-6V0C-RB-WF | CONN HEADER 30POS SMT VERT 30AU
JETSON1:JETSON_TX2_J21_EXPANSION1:U1 | NXP Semiconductors | PCF8574ATD-T | Smt t/r
JETSON1:X1 | Phoenix Contact | 43045-0209 | CONN HEADER 2POS RT ANG SMD TIN
MICROCONTROLLER1:LED1 | Chicago Miniature Lighting | CMD17-21VGD/TR8 | Led, Green, 1.25mm x 1.4mm, 7mcd, 570nm, Full Reel
MICROCONTROLLER1:LED2 | Chicago Miniature Lighting | CMD17-21VGD/TR8 | Led, Green, 1.25mm x 1.4mm, 7mcd, 570nm, Full Reel
MICROCONTROLLER1:LED3 | Chicago Miniature Lighting | CMD17-21VGD/TR8 | Led, Green, 1.25mm x 1.4mm, 7mcd, 570nm, Full Reel
MICROCONTROLLER1:LED4 | Chicago Miniature Lighting | CMD17-21VGD/TR8 | Led, Green, 1.25mm x 1.4mm, 7mcd, 570nm, Full Reel
MICROCONTROLLER1:LED5 | Chicago Miniature Lighting | CMD17-21VGD/TR8 | Led, Green, 1.25mm x 1.4mm, 7mcd, 570nm, Full Reel
MICROCONTROLLER1:LED6 | Chicago Miniature Lighting | CMD17-21VGD/TR8 | Led, Green, 1.25mm x 1.4mm, 7mcd, 570nm, Full Reel
MICROCONTROLLER1:LED7 | Chicago Miniature Lighting | CMD17-21VGD/TR8 | Led, Green, 1.25mm x 1.4mm, 7mcd, 570nm, Full Reel
MICROCONTROLLER1:LED8 | Chicago Miniature Lighting | CMD17-21VGD/TR8 | Led, Green, 1.25mm x 1.4mm, 7mcd, 570nm, Full Reel
MICROCONTROLLER1:R1 | Yageo | RC0603FR-0760R4L | RES SMD 60.4 OHM 1% 1/10W 0603
MICROCONTROLLER1:R2 | Yageo | RC0603FR-0760R4L | RES SMD 60.4 OHM 1% 1/10W 0603
MICROCONTROLLER1:R3 | Yageo | RC0603FR-0760R4L | RES SMD 60.4 OHM 1% 1/10W 0603
MICROCONTROLLER1:R4 | Yageo | RC0603FR-0760R4L | RES SMD 60.4 OHM 1% 1/10W 0603
MICROCONTROLLER1:R5 | Yageo | RC0603FR-0760R4L | RES SMD 60.4 OHM 1% 1/10W 0603
MICROCONTROLLER1:R6 | Yageo | RC0603FR-0760R4L | RES SMD 60.4 OHM 1% 1/10W 0603
MICROCONTROLLER1:R7 | Yageo | RC0603FR-0760R4L | RES SMD 60.4 OHM 1% 1/10W 0603
MICROCONTROLLER1:R8 | Yageo | RC0603FR-0760R4L | RES SMD 60.4 OHM 1% 1/10W 0603
MICROCONTROLLER1:R9 | Yageo | RC0603FR-0710KL | RES SMD 10K OHM 1% 1/10W 0603
MICROCONTROLLER1:R10 | Yageo | RC0603FR-0710KL | RES SMD 10K OHM 1% 1/10W 0603
MICROCONTROLLER1:U$1
MICROCONTROLLER1:U1 | NXP Semiconductors | PCF8574ATD-T | Smt t/r
MOTOR_TOP1:JDL | Phoenix Contact | 43045-0609 | CONN HEADER 6POS RT ANG SMD TIN
MOTOR_TOP1:JDR | Phoenix Contact | 43045-0609 | CONN HEADER 6POS RT ANG SMD TIN
MOTOR_TOP1:X3 | Phoenix Contact | 43045-0609 | CONN HEADER 6POS RT ANG SMD TIN
MOTOR_TOP1:X4 | Phoenix Contact | 43045-0609 | CONN HEADER 6POS RT ANG SMD TIN
MOTOR_TOP1:X5 | Phoenix Contact | 43045-0609 | CONN HEADER 6POS RT ANG SMD TIN
MOTOR_TOP1:X6 | Molex | 43045-0409 | CONN HEADER 4POS RT ANG SMD TIN
MOTOR_TOP1:X7 | Molex | 43045-0409 | CONN HEADER 4POS RT ANG SMD TIN
MOTOR_TOP1:X8 | Molex | 43045-0409 | CONN HEADER 4POS RT ANG SMD TIN
POWER_TOP1:C1 | Taiyo Yuden | TMK107BJ105KA-T | CAP CER 1UF 25V X5R 0603
POWER_TOP1:C2 | Murata | GRM188R61E106MA73D | CAP CER 10UF 25V X5R 0603
POWER_TOP1:C3 | Taiyo Yuden | TMK107BJ105KA-T | CAP CER 1UF 25V X5R 0603
POWER_TOP1:C4 | Murata | GRM188R61E106MA73D | CAP CER 10UF 25V X5R 0603
POWER_TOP1:F1 | Littelfuse | 0154003.DR | Fuse Chip Very Fast Acting 4A SMD Solder Pad 9.73 X 5.03 X 3.81mm T/R CSA/PSE/UL
POWER_TOP1:F2 | Littelfuse | 0154003.DR | Fuse Chip Very Fast Acting 4A SMD Solder Pad 9.73 X 5.03 X 3.81mm T/R CSA/PSE/UL
POWER_TOP1:LED1 | Chicago Miniature Lighting | CMD17-21VGD/TR8 | Led, Green, 1.25mm x 1.4mm, 7mcd, 570nm, Full Reel
POWER_TOP1:LED2 | Chicago Miniature Lighting | CMD17-21VGD/TR8 | Led, Green, 1.25mm x 1.4mm, 7mcd, 570nm, Full Reel
POWER_TOP1:LED3 | Chicago Miniature Lighting | CMD17-21VGD/TR8 | Led, Green, 1.25mm x 1.4mm, 7mcd, 570nm, Full Reel
POWER_TOP1:MOV1 | TDK Corporation | AVR-M2012C120MT6AB | VARISTOR 12V 60A 0805
POWER_TOP1:MOV2 | Avx | VC080503A100DP | VARISTOR 5V 40A 0805
POWER_TOP1:R2 | Yageo | RC0603FR-07470RL | RES SMD 470 OHM 1% 1/10W 0603
POWER_TOP1:R3 | Yageo | RC0603FR-07147RL | RES SMD 147 OHM 1% 1/10W 0603
POWER_TOP1:R4 | Yageo | RC0603JR-072KL | RES SMD 2K OHM 5% 1/10W 0603
POWER_TOP1:U$1 | Recom | R-725.0P | CONV DC/DC 2A 6.5-28VIN 5V
POWER_TOP1:U$2 | Delta Electronics | V36SE12004NRFA | MODULE DC/DC 1/16 BRICK 12V 4A
RC_INPUT1:U1 | Fairchild Semiconductor | NC7SZ04M5 | NC7SZ04 Series 5.5 V Surface Mount TinyLogic UHS Inverter - SOT-23-5
RC_INPUT1:X1 | Molex | 43045-0409 | CONN HEADER 4POS RT ANG SMD TIN
RELAY_CONTROL_TOP1:D2 | STMicroelectronics | STPS20M60D | SCHOTTKY 60V 20A
RELAY_CONTROL_TOP1:FH3 | LittelFuse | 01000020Z | 2x FUSE CLIP CARTRIDGE 600V 20A PCB
RELAY_CONTROL_TOP1:ISO1:R1 | Yageo | RC0603FR-0747KL | RES SMD 47K OHM 1% 1/10W 0603
RELAY_CONTROL_TOP1:ISO1:R2 | Yageo | RC0603FR-07330KL | RES SMD 330K OHM 1% 1/10W 0603
RELAY_CONTROL_TOP1:ISO1:R3 | Yageo | RC0603JR-072KL | RES SMD 2K OHM 5% 1/10W 0603
RELAY_CONTROL_TOP1:ISO1:R4 | Yageo | RC0603JR-072KL | RES SMD 2K OHM 5% 1/10W 0603
RELAY_CONTROL_TOP1:ISO1:R5 | Yageo | RC0603FR-07330KL | RES SMD 330K OHM 1% 1/10W 0603
RELAY_CONTROL_TOP1:ISO1:R6 | Yageo | RC0603JR-072KL | RES SMD 2K OHM 5% 1/10W 0603
RELAY_CONTROL_TOP1:ISO1:U1 | Texas Instruments | AMC1200SDUB | IC OPAMP ISOLATION 100KHZ 8SOP
RELAY_CONTROL_TOP1:ISO1:U2 | Vishay Semiconductor | SFH615A-3X009T | Optocoupler DC-IN 1-CH Transistor DC-OUT 4-Pin PDIP SMD T/R
RELAY_CONTROL_TOP1:JBAT | Phoenix Contact | 43045-0209 | CONN HEADER 2POS RT ANG SMD TIN
RELAY_CONTROL_TOP1:JDC | Phoenix Contact | 43045-0209 | CONN HEADER 2POS RT ANG SMD TIN
RELAY_CONTROL_TOP1:JISO | Phoenix Contact | 43045-0209 | CONN HEADER 2POS RT ANG SMD TIN
RELAY_CONTROL_TOP1:JMC | Phoenix Contact | 43045-0209 | CONN HEADER 2POS RT ANG SMD TIN
RELAY_CONTROL_TOP1:MOV1 | EPCOS | B72220S0200K101 | VARISTOR 33V 2KA DISC 20MM
RELAY_CONTROL_TOP1:R1 | Yageo | RC2512JK-070RL | RES SMD 0 OHM JUMPER 1W 2512
RELAY_CONTROL_TOP1:R2 | Yageo | RC2512JK-070RL | RES SMD 0 OHM JUMPER 1W 2512
RELAY_CONTROL_TOP1:REGULATOR1:U1 | Texas Instruments | LM2936HVMAX5.0NOPB | IC REG LINEAR 5V 50MA 8SOIC
RELAY_CONTROL_TOP1:RELAY_CONTROL1:D1 | SMC | 1N4148WSTR | DIODE GEN PURP 75V 300MA SOD323
RELAY_CONTROL_TOP1:RELAY_CONTROL1:D2 | SMC | 1N4148WSTR | DIODE GEN PURP 75V 300MA SOD323
RELAY_CONTROL_TOP1:RELAY_CONTROL1:JESTP | Phoenix Contact | 43045-0209 | CONN HEADER 2POS RT ANG SMD TIN
RELAY_CONTROL_TOP1:RELAY_CONTROL1:JMOW | Phoenix Contact | 43045-0209 | CONN HEADER 2POS RT ANG SMD TIN
RELAY_CONTROL_TOP1:RELAY_CONTROL1:JTHR | Phoenix Contact | 43045-0209 | CONN HEADER 2POS RT ANG SMD TIN
RELAY_CONTROL_TOP1:RELAY_CONTROL1:R1 | Yageo | RC0603JR-072KL | RES SMD 2K OHM 5% 1/10W 0603
RELAY_CONTROL_TOP1:RELAY_CONTROL1:R3 | Yageo | RC0603JR-072KL | RES SMD 2K OHM 5% 1/10W 0603
RELAY_CONTROL_TOP1:RELAY_CONTROL1:R11 | Yageo | RC0603FR-0747KL | RES SMD 47K OHM 1% 1/10W 0603
RELAY_CONTROL_TOP1:RELAY_CONTROL1:R13 | Yageo | RC0603FR-0747KL | RES SMD 47K OHM 1% 1/10W 0603
RELAY_CONTROL_TOP1:RELAY_CONTROL1:RCCB1 | Rohm | MCR100JZHF52R3 | RES SMD 52.3 OHM 1% 1W 2512
RELAY_CONTROL_TOP1:RELAY_CONTROL1:RCCB2 | Rohm | MCR100JZHF52R3 | RES SMD 52.3 OHM 1% 1W 2512
RELAY_CONTROL_TOP1:RELAY_CONTROL1:RCCD | Rohm | MCR100JZHF52R3 | RES SMD 52.3 OHM 1% 1W 2512
RELAY_CONTROL_TOP1:RELAY_CONTROL1:RCCM | Rohm | MCR100JZHF52R3 | RES SMD 52.3 OHM 1% 1W 2512
RELAY_CONTROL_TOP1:RELAY_CONTROL1:U$2 | Diodes Inc | ZXTN25100DGTA | TRANS NPN 100V 3A SOT223
RELAY_CONTROL_TOP1:RELAY_CONTROL1:U$7 | Diodes Inc | ZXTN25100DGTA | TRANS NPN 100V 3A SOT223
RELAY_CONTROL_TOP1:RELAY_CONTROL1:U$10 | Diodes Inc | ZXTN25100DGTA | TRANS NPN 100V 3A SOT223
RELAY_CONTROL_TOP1:RELAY_CONTROL1:UVLO1:R1 | Yageo | RC0603FR-07750KL | RES SMD 750K OHM 1% 1/10W 0603
RELAY_CONTROL_TOP1:RELAY_CONTROL1:UVLO1:R2 | Yageo | RC0603FR-07150KL | RES SMD 150K OHM 1% 1/10W 0603
RELAY_CONTROL_TOP1:RELAY_CONTROL1:UVLO1:R3 | Yageo | RC0603FR-07180KL | RES SMD 180K OHM 1% 1/10W 0603
RELAY_CONTROL_TOP1:RELAY_CONTROL1:UVLO1:R4 | Yageo | RC0603FR-0747KL | RES SMD 47K OHM 1% 1/10W 0603
RELAY_CONTROL_TOP1:RELAY_CONTROL1:UVLO1:R7 | Yageo | RC0603FR-0747KL | RES SMD 47K OHM 1% 1/10W 0603
RELAY_CONTROL_TOP1:RELAY_CONTROL1:UVLO1:R8 | Yageo | RC0603FR-07330KL | RES SMD 330K OHM 1% 1/10W 0603
RELAY_CONTROL_TOP1:RELAY_CONTROL1:UVLO1:U1 | Texas Instruments | LMV762MM/NOPB | Low Voltage, Precision Comparator with Push-Pull Output 8-VSSOP -40 to 125
SENSOR_TOP1:ENCODER1:X1 | Phoenix Contact | 1751264 | CONN TERM BLOCK 4POS 3.5MM
SENSOR_TOP1:ENCODER2:X1 | Phoenix Contact | 1751264 | CONN TERM BLOCK 4POS 3.5MM
SENSOR_TOP1:IMU1:U$1 | Sparkfun | LSM9DS1-Breakout | 9DoF IMU Breakout
SENSOR_TOP1:REACH_GPS1:U$1 | Hirose | DF13-6P-1.25V(50) | CONN HEADER 6POS 1.25MM SMD GOLD
SENSOR_TOP1:U1 | Push- Pull 14-TSSOP -40 to 125 | Texas Instruments | 4-Bit Bidirectional Multi-Voltage Level Translator for Open-Drain &amp

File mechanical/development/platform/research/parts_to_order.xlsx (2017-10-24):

Part No | MFG | Description | Price | QTY | Sub Total | Weight | Link
GLM801600 | GreenWorks | GreenWorks Pro GLM801602 80V 21-Inch Cordless Lawn Mower, 4AH Battery and a Charger Included | $499.00 | 1
TD-111-135 | SuperDroid Robots | Wheelchair Motors and Encoders | $897.00 | 1 | $897.00 | 31 | https://www.superdroidrobots.com/shop/item.aspx/dg-158a-24vdc-135-rpm-wheel-chair-motor-pair/1531/
SB2425 | Smart Battery | 24V 25 aH Battery | $699.98 | 1 | $699.98 | 18 | https://www.lithiumion-batteries.com/products/24-volt-lithium-batteries/24v-25ah-lithium-ion-battery.php
DP-RS2 | Smart Battery | Battery Charger | $164.99 | 1 | $164.99 | 0.5 | https://www.lithiumion-batteries.com/products/lithium-ion-chargers/24v-lithium-ion-battery-chargers/dual-bank-6-amp-charger.php
TE-240-030 | SuperDroid Robots | Motor Controller | $328.91 | 1 | $328.91 | 0.5 | https://www.superdroidrobots.com/shop/item.aspx/roboteq-mdc2230-2x60a-30v-motor-controller-with-encoder-input/1833/
TD-178-000 | SuperDroid Robots | 13" tiller tires and mounting | $148.80 | 1 | $148.80 | 16 | https://www.superdroidrobots.com/shop/item.aspx/direct-drive-wheelchair-motor-wheel-and-shaft-set-pair-13-inch-traction-lug/2237/
S-5210-PRB | Caster Connection | 10" Pneumatic Swivel Caster | $67.63 | 1 | $67.63 | 12 | https://casterconnection.com/s-5210-prb.html
 |  | NVIDIA Jetson TX2 Dev Kit | $560.00 | 1 | $560.00 | 0.1 | https://www.amazon.com/NVIDIA-Jetson-TX2-Development-Kit/dp/B06XPFH939
Misc Item Extrusion | Item | Misc Mechanical Parts | $1100.00 | 1 | $1100.00 | 5
Misc Fasteners | McMaster-Carr | Misc Electrical Parts | $500.00 | 1 | $500.00 | 2
 |  |  |  |  | $0.00
 |  |  |  |  | $4467.31 | 85.1
 |  |  |  |  | 900
 |  |  |  |  | 330
 |  |  |  |  | 150
 |  |  |  |  | 70
 |  |  |  |  | 700
 |  |  |  |  | 165
 |  |  |  |  | 560
 |  |  |  |  | 400
 |  |  |  |  | 500
 |  |  |  |  | 600
 |  |  |  |  | 4375

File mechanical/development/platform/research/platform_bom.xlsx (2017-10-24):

Part No | MFG | Description | Price | QTY | Sub Total | Weight | Link
4.5"x9"x0.375" plate |  |  |  | 2 | $0.00

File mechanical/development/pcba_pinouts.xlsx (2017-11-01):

Integration Board | QTY | Connector Type | MFG | PCB Part # | Additional Part #s | Additional Part #s | Mating Connector Part # | Additional Mating Part #s | Josh's Notes:
2x20 2.54 mm latching connector & cable for the arduino breakouts | 2 | Latching shrouded header | 3M | N2540-6V0C-RB-WG | 3505-33B | 3505-8140 | 89140-0103 | 3302/40-CUT-LENGTH | I used a vertical instead of right angle header because the ribbon cable will extend off the board at a right angle with a vertical header.
Encoder 4 pins - screw terminal | 2 | screw terminal | Phoenix Contact | 1778780 |  |  | 1778858
Motor - 5 pins for motor driver | 2 | microfit pre-made cables | Molex | 43045-0609 |  |  | 245132-0620
Deck Control 6 pins | 3 | microfit pre-made cables | Molex | 43045-0609 |  |  | 245132-0620
RC Input - pwr gnd sbus 3 pins total | 1 | microfit pre-made cables | Molex | 43045-0409 |  |  | 245132-0420 |  | Using a 4 pin connector for a 3 pin application so we can use the nice overmolded cables
Jetson GPIO pins 2x15 2.54 mm header row for the TX2 I/O In | 1 | latching shrouded header | 3M | N2530-6V0C-RB-WF | 3505-33B | 3505-8130 | 89130-0103 | 3302/40-CUT-LENGTH | NOTE: Order 40 wire cable, peel to 30 wires. I used a vertical instead of right angle header because the ribbon cable will extend off the board at a right angle with a vertical header.
2x20 2.54 mm latching connector & cable for the TX2 expansion breakouts | 2 | latching shrouded header | 3M | N2540-6V0C-RB-WG | 3505-33B | 3505-8140 | 89140-0103 | 3302/40-CUT-LENGTH | I used a vertical instead of right angle header because the ribbon cable will extend off the board at a right angle with a vertical header.
UART - 3 pins - GND, TX, RX and 5V out to GPS | 1 | microfit pre-made cables | Molex | 43045-0409 |  |  | 245132-0420 |  | Using a 4 pin connector for a 3 pin application so we can use the nice overmolded cables
E-stop connector 2 pins | 2 | microfit pre-made cables | Molex | 43045-0209 |  |  | 245132-0220
2 position - send 12 volts from board to jetson | 1 | microfit pre-made cables | Molex | 43045-0209 |  |  | 245132-0220
receive 36 volts from fuse | 1 | microfit pre-made cables | Phoenix Contact | 1814919 |  |  | 1704853 |  | Going with a white connector here to differentiate from all the other black connectors since this is 36V Power Input
2 position connector for mower relay coil | 1 | microfit pre-made cables | Molex | 43045-0209 |  |  | 245132-0220
2 position connector for drive motor relay coil (killed after DC DC converter | 1 | microfit pre-made cables | Molex | 43045-0209 |  |  | 245132-0220
2 position connector for linear motor relay coil | 1 | microfit pre-made cables | Molex | 43045-0209 |  |  | 245132-0220
Mandatory DIN rail Stuff
Spec out a 30 amp fuse 36 V on din rail | 1
25 A relay for din rail | 1
25 A fuse to mower | 1
16 A fuse to DC DC converter to drive motor | 1
16 A relay for DC Motors after DC DC converter | 1
OPTIONAL DIN RAIL STUFF
12 V 9 A relay for linear motors | 1
9A fuse for linear motors | 1
Terminal blocks for linear motors?
36V to 12V power converter for linear motors | 1

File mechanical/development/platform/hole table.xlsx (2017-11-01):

TAG | X LOC | Y LOC | SIZE
A1 | 13/64" | 23/8" | n 9/64" THRU ALL 8-32 UNC THRU ALL
A2 | 13/64" | 731/64" | n 9/64" THRU ALL 8-32 UNC THRU ALL
A3 | 451/64" | 23/8" | n 9/64" THRU ALL 8-32 UNC THRU ALL
A4 | 451/64" | 731/64" | n 9/64" THRU ALL 8-32 UNC THRU ALL
A5 | 11/32" | 933/64" | n 9/64" THRU ALL 8-32 UNC THRU ALL
A6 | 11/32" | 1013/64" | n 9/64" THRU ALL 8-32 UNC THRU ALL
A7 | 11/32" | 133/16" | n 9/64" THRU ALL 8-32 UNC THRU ALL
A8 | 111/32" | 11/32" | n 9/64" THRU ALL 8-32 UNC THRU ALL
A9 | 143/64" | 1041/64" | n 9/64" THRU ALL 8-32 UNC THRU ALL
A10 | 223/64" | 12" | n 9/64" THRU ALL 8-32 UNC THRU ALL
A11 | 223/64" | 145/8" | n 9/64" THRU ALL 8-32 UNC THRU ALL
A12 | 31/16" | 1041/64" | n 9/64" THRU ALL 8-32 UNC THRU ALL
A13 | 47/64" | 933/64" | n 9/64" THRU ALL 8-32 UNC THRU ALL
A14 | 423/64" | 1013/64" | n 9/64" THRU ALL 8-32 UNC THRU ALL
A15 | 423/64" | 133/16" | n 9/64" THRU ALL 8-32 UNC THRU ALL
A16 | 511/32" | 11/32" | n 9/64" THRU ALL 8-32 UNC THRU ALL
A17 | 511/32" | 459/64" | n 9/64" THRU ALL 8-32 UNC THRU ALL
A18 | 511/32" | 853/64" | n 9/64" THRU ALL 8-32 UNC THRU ALL
A19 | 617/64" | 83/8" | n 9/64" THRU ALL 8-32 UNC THRU ALL
A20 | 645/64" | 11/32" | n 9/64" THRU ALL 8-32 UNC THRU ALL
A21 | 741/64" | 83/8" | n 9/64" THRU ALL 8-32 UNC THRU ALL
A22 | 77/8" | 933/64" | n 9/64" THRU ALL 8-32 UNC THRU ALL
A23 | 77/8" | 1013/64" | n 9/64" THRU ALL 8-32 UNC THRU ALL
A24 | 77/8" | 1315/64" | n 9/64" THRU ALL 8-32 UNC THRU ALL
A25 | 77/8" | 1359/64" | n 9/64" THRU ALL 8-32 UNC THRU ALL
A26 | 125/64" | 11/32" | n 9/64" THRU ALL 8-32 UNC THRU ALL
A27 | 135/64" | 111/32" | n 9/64" THRU ALL 8-32 UNC THRU ALL
A28 | 135/64" | 633/64" | n 9/64" THRU ALL 8-32 UNC THRU ALL
A29 | 135/64" | 1315/64" | n 9/64" THRU ALL 8-32 UNC THRU ALL
A30 | 135/64" | 1359/64" | n 9/64" THRU ALL 8-32 UNC THRU ALL
B1 | 29/64" | 29/64" | 3/8 THRU ALL
B2 | 61/64" | 1461/64" | 3/8 THRU ALL
B3 | 1229/64" | 1461/64" | 3/8 THRU ALL
B4 | 1261/64" | 29/64" | 3/8 THRU ALL
D1 | 5" | 109/64" | n 3/32" THRU ALL 4-40 UNC THRU ALL
D2 | 5" | 129/64" | n 3/32" THRU ALL 4-40 UNC THRU ALL
D3 | 5" | 1235/64" | n 3/32" THRU ALL 4-40 UNC THRU ALL
D4 | 5" | 1435/64" | n 3/32" THRU ALL 4-40 UNC THRU ALL
D5 | 67/64" | 11/16" | n 3/32" THRU ALL 4-40 UNC THRU ALL
D6 | 67/64" | 711/64" | n 3/32" THRU ALL 4-40 UNC THRU ALL
D7 | 71/4" | 109/64" | n 3/32" THRU ALL 4-40 UNC THRU ALL
D8 | 71/4" | 129/64" | n 3/32" THRU ALL 4-40 UNC THRU ALL
D9 | 71/4" | 1235/64" | n 3/32" THRU ALL 4-40 UNC THRU ALL
D10 | 71/4" | 1435/64" | n 3/32" THRU ALL 4-40 UNC THRU ALL
D11 | 851/64" | 815/64" | n 3/32" THRU ALL 4-40 UNC THRU ALL
D12 | 851/64" | 1263/64" | n 3/32" THRU ALL 4-40 UNC THRU ALL
D13 | 125/32" | 815/64" | n 3/32" THRU ALL 4-40 UNC THRU ALL
D14 | 125/32" | 1263/64" | n 3/32" THRU ALL 4-40 UNC THRU ALL
D15 | 125/16" | 11/16" | n 3/32" THRU ALL 4-40 UNC THRU ALL
D16 | 125/16" | 617/64" | n 3/32" THRU ALL 4-40 UNC THRU ALL

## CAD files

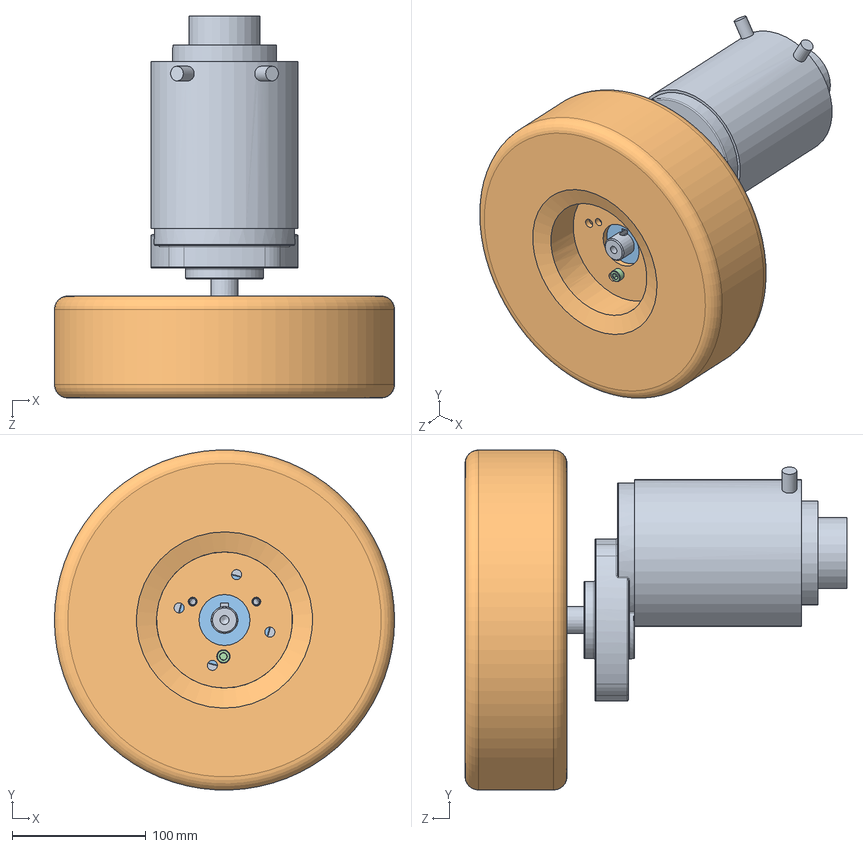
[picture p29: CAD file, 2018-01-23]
mechanical/development/platform/wheel_assembly_2.SLDASM
254.0 x 253.8 x 285.2 mm
amer_mrp17_no_brake
TD-109-010
9604T17
91292A135

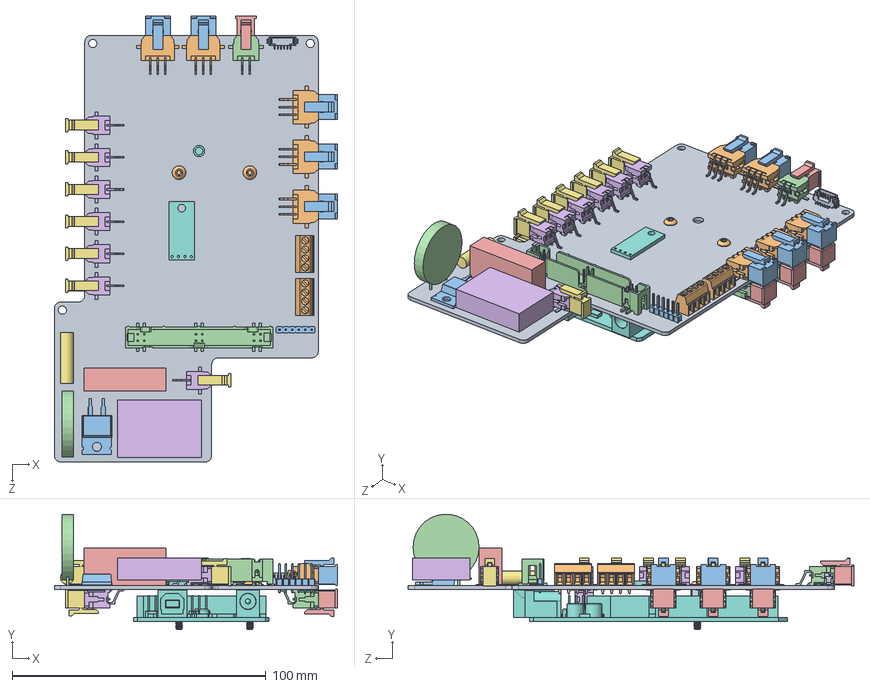
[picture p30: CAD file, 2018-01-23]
mechanical/development/platform/breakout_board.SLDASM
111.7 x 45.4 x 175.7 mm
arduino_board
ArduinoMega
91075A472 x 2
92949A106 x 2
STPS20M60D
MOV-20D470K
R-745.0P
V36SE12004NRFA-TH
LF445_0.807IN
LSM9DS1_Sparkfun
DF13C-6P-1.25V
STEP-61300611121-rev1
N2540-6V0C-RB-WG

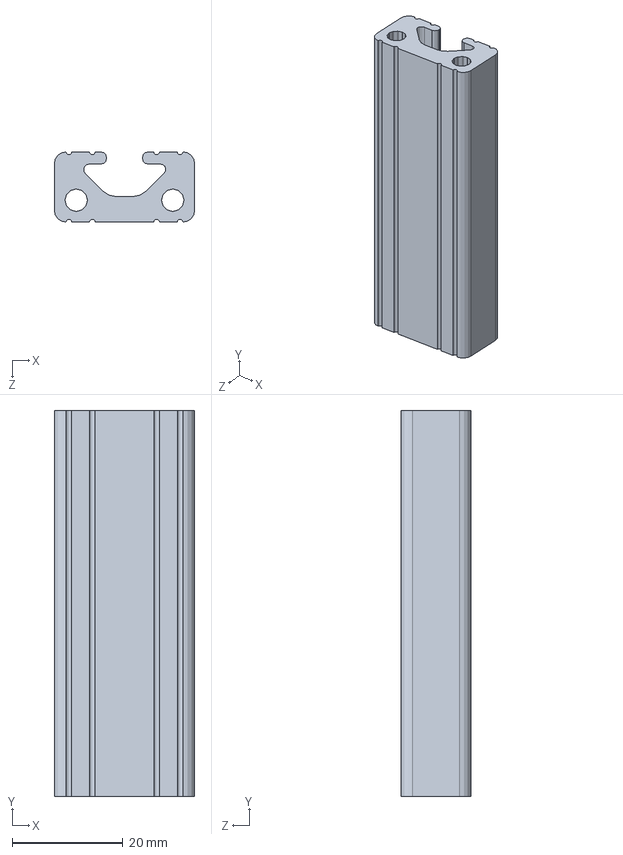
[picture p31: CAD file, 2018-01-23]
mechanical/development/platform/Antenna_holder.SLDASM
25.4 x 69.8 x 12.7 mm

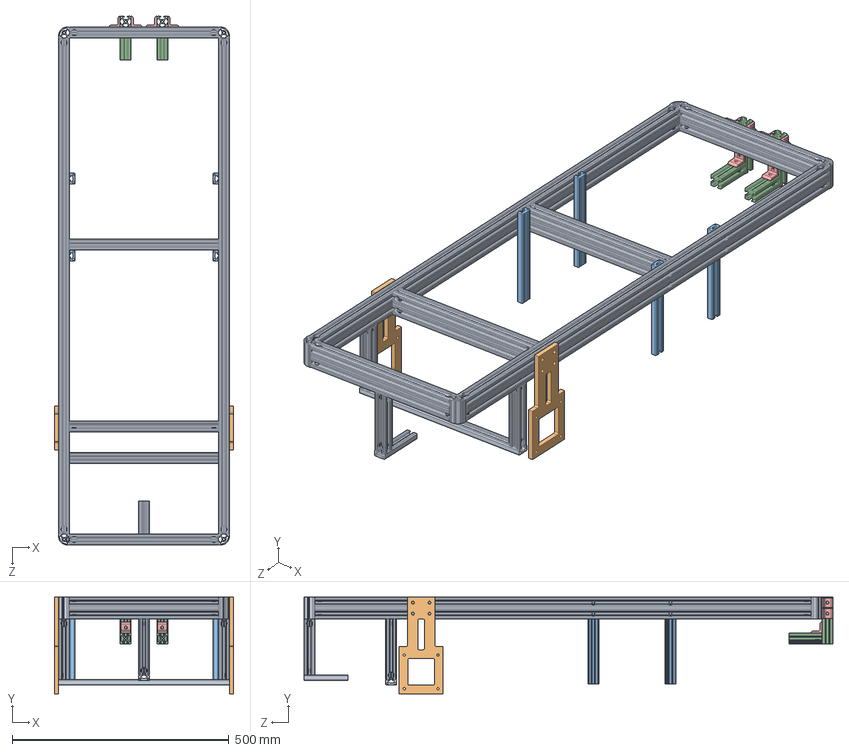
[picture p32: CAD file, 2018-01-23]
mechanical/development/platform/frame_assembly.SLDASM
412.8 x 223.2 x 1219.2 mm
new_main_frame
bracket_motor x 2
deck_height_extrusion x 4
vertical_extrusion
47065T236 x 10
47065T153

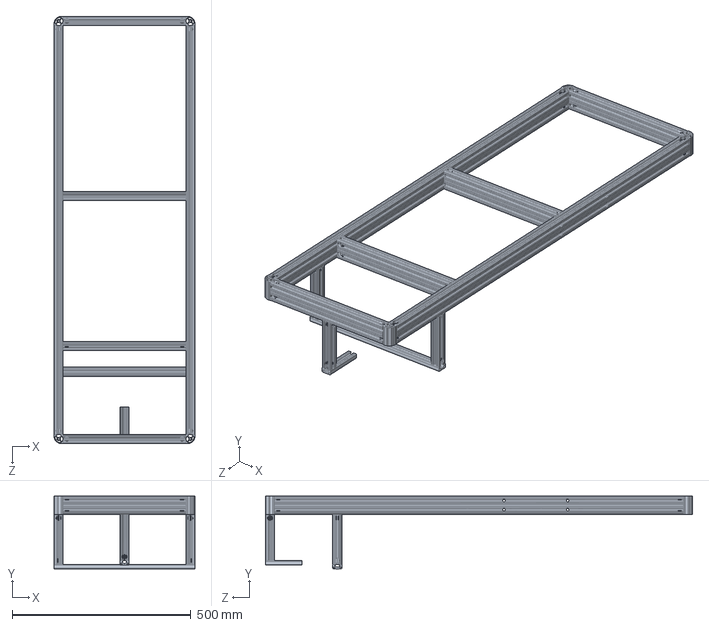
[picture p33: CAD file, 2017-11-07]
mechanical/development/platform/new_main_frame.SLDPRT
393.7 x 203.2 x 1193.8 mm

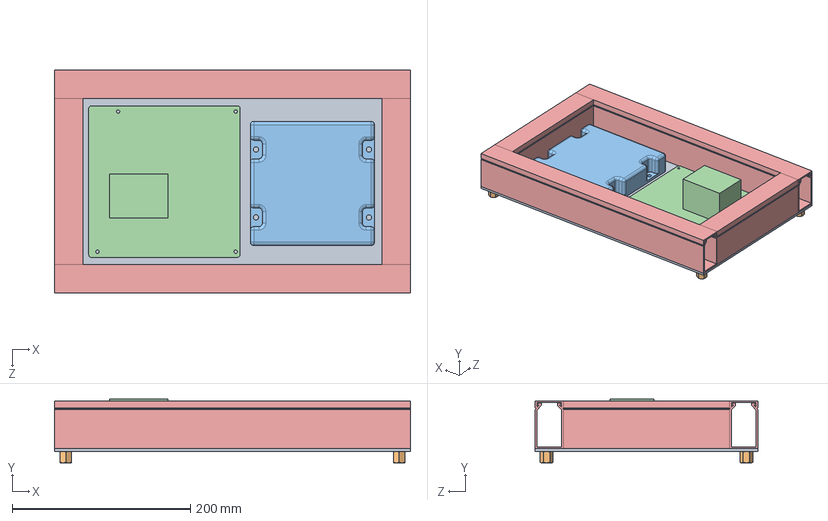
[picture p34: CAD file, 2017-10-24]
mechanical/development/platform/electrical_panel.SLDASM
400.0 x 71.5 x 250.0 mm
main_electrical_panel
91115A403 x 4
TE-240-030
jetson_tx2_dev_kit
duct

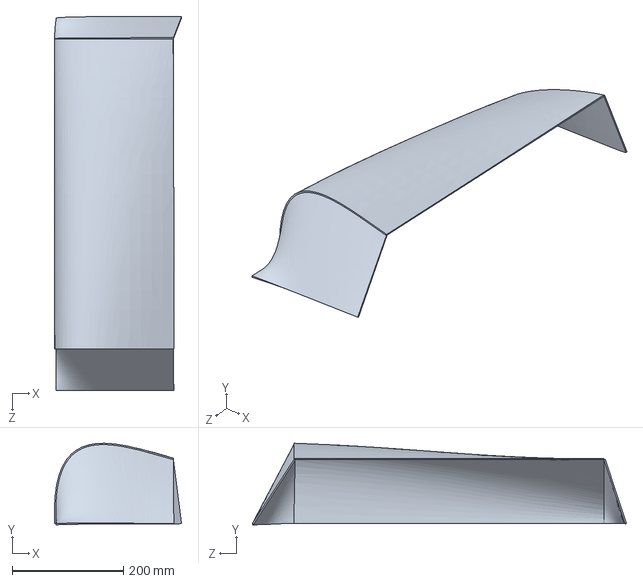
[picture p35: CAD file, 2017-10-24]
mechanical/development/platform/main_cover.SLDPRT
228.3 x 146.5 x 671.3 mm

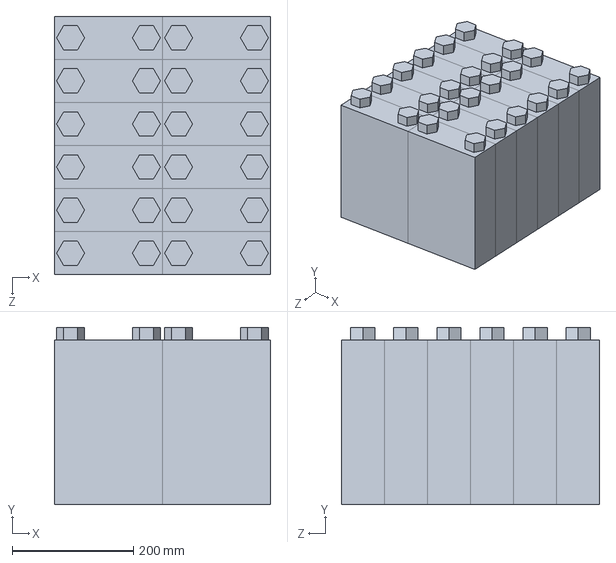
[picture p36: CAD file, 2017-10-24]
mechanical/development/platform/36v_battery.SLDASM
356.0 x 292.0 x 426.0 mm
3v_cell x 12

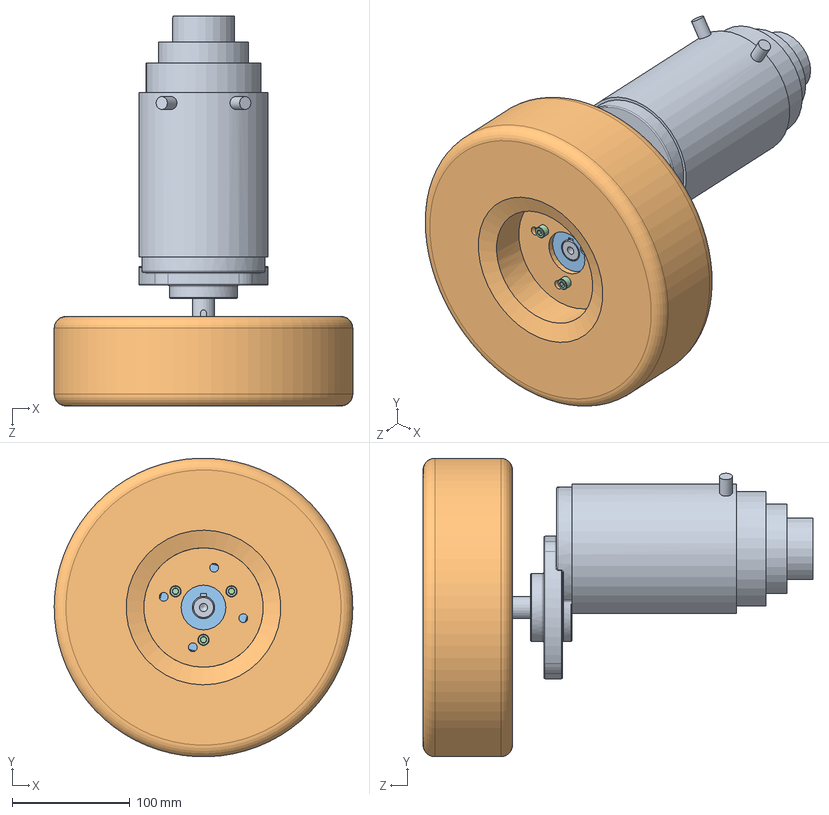
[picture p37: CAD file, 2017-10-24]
mechanical/development/platform/wheel_assembly.SLDASM
254.0 x 253.8 x 331.7 mm
amer_mrp17
9684T3
92196A652 x 3

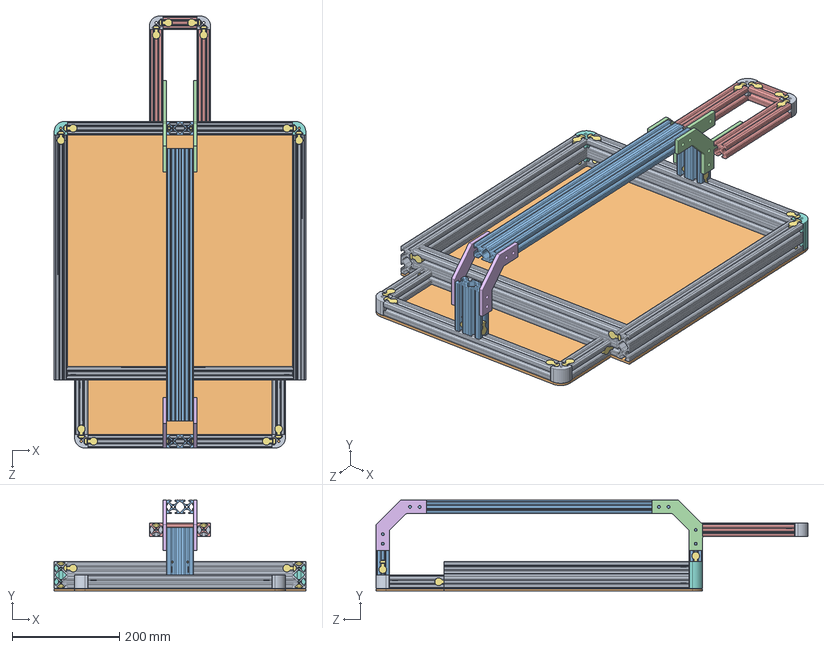
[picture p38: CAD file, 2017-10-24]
mechanical/development/platform/chassis_subassembly.SLDASM
469.9 x 169.4 x 806.5 mm
main_frame
top_frame
caster_angle_bracket x 2
caster_bracket_frame
caster_rear angle_bracket x 2
47065T153 x 26
corner_extrusion x 2
corner_extrusion_1_inch x 4

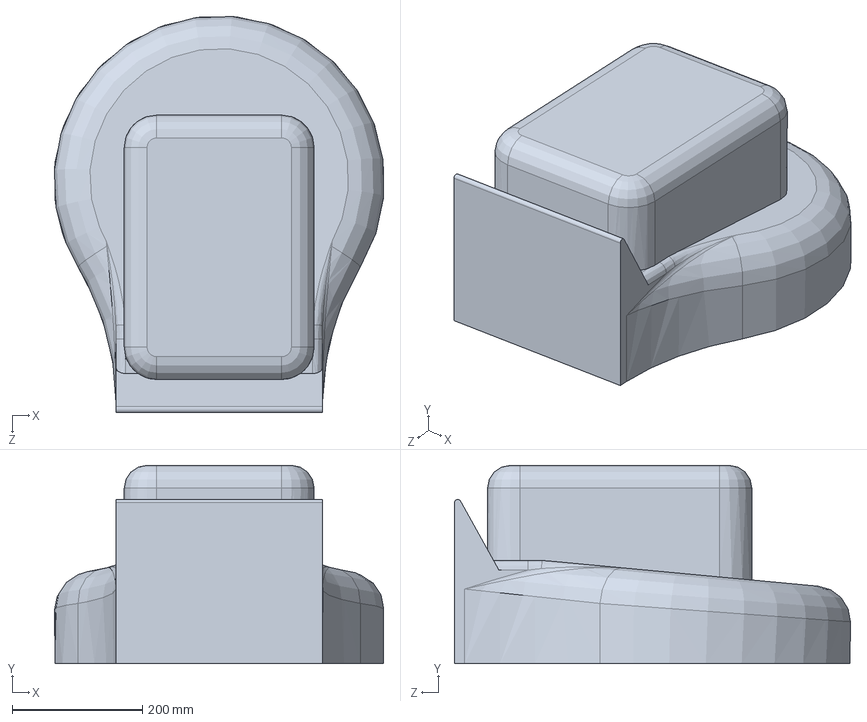
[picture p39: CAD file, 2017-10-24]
mechanical/development/platform/mower.SLDASM
506.4 x 304.8 x 608.8 mm

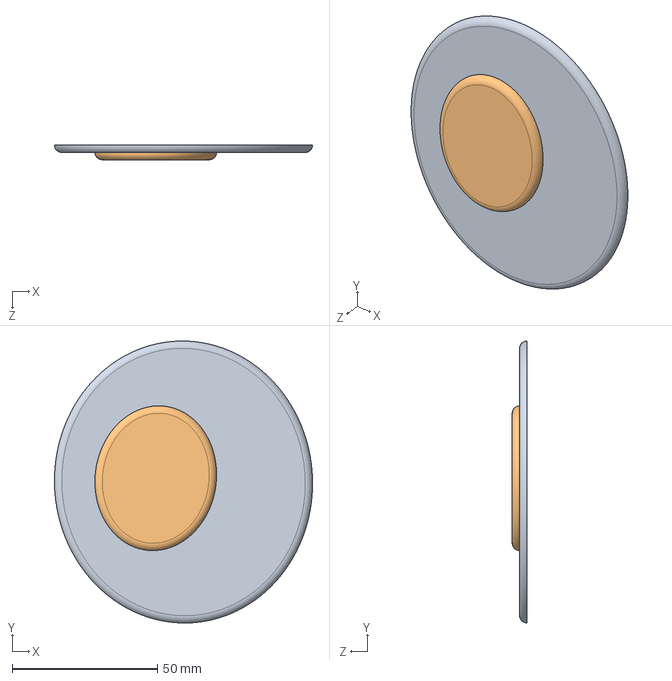
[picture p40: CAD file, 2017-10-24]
mechanical/development/platform/googlyeyes.SLDASM
88.9 x 97.1 x 5.08 mm
Googly Eye Base
googlyeyepupil

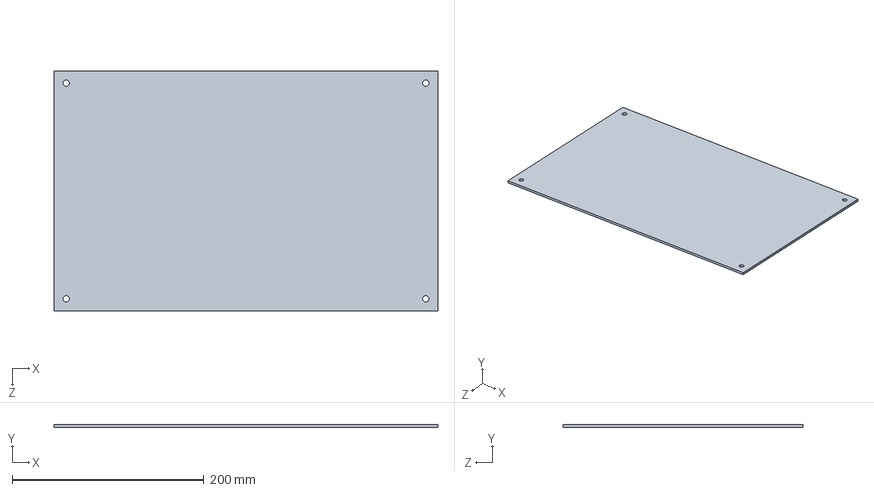
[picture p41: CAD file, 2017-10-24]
mechanical/development/platform/main_electrical_panel.SLDPRT
400.0 x 3.17 x 250.0 mm

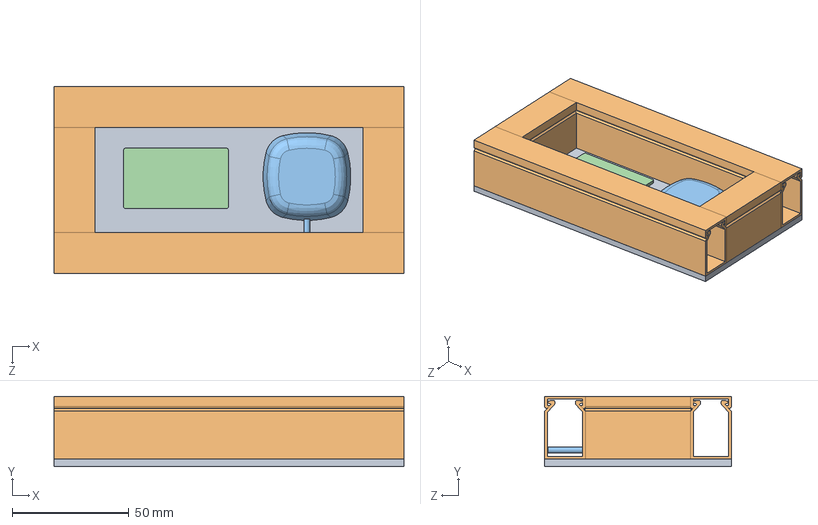
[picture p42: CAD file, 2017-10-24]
mechanical/development/platform/sensor_electrical_panel.SLDASM
150.0 x 30.1 x 80.0 mm
sensor_electrical_panel
sensor_duct
gps_rtk_transceiver
gps_rtk_board

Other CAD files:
mechanical/development/platform/main_dxf_3.SLDPRT
mechanical/development/platform/main_cover1.SLDPRT
mechanical/development/platform/electrical_panel_grudsby_v2.SLDASM
mechanical/development/platform/main_frame.SLDPRT
electrical/dxf/arduino_mega_position.DXF
electrical/dxf/breakout_board.DXF
electrical/dxf/breakout_board_bottom_conn_pos.DXF
electrical/dxf/breakout_board_bottom_keepout.DXF
electrical/dxf/breakout_board_top_conn_pos.DXF
electrical/dxf/breakout_board_top_keepout.DXF
mechanical/development/platform/1704853_00.SLDPRT
mechanical/development/platform/1751264_04.SLDPRT
mechanical/development/platform/1778780.SLDPRT
mechanical/development/platform/1778858.SLDPRT
mechanical/development/platform/1814919_00.SLDPRT
mechanical/development/platform/22925T11.SLDPRT
mechanical/development/platform/22925T17.SLDPRT
mechanical/development/platform/22925T17_assy.SLDASM
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

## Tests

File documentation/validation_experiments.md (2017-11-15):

System Validation Experiments

Fall Validation Experiment

	The aim of the fall validation experiment is to test individual subsystems. As such many of the systems requirements set for GroundsBot will not be fully met. All tests to be performed have been designed to indicate significant progress towards reaching the system requirements. More specifically the team plans to test the base functionality of the mobility, localization, planning, and perception subsystems of GroundsBot. The details of the test are laid out below.

Test 1:
  Purpose: Test GroundsBot's ability to navigate repeatably using GPS and odometry
  Location: Field by Doherty Apartments
  Equipment: GroundsBot, GroundsBot base station, laptop, GPS waypoints for test field, boundary creation app, 5 flags, GroundsBot remote control
  Pre-test setup: 

      Create GPS waypoints using app (following a typical zigzag pattern a groundskeeper might make when mowing a lawn)

      Power on GroundsBot  
      
      Navigate GroundsBot to an arbitrary home position and orientation on test field using remote control
      
      Place flag by home position

      Establish connection between GroundsBot and laptop

      Send GPS waypoints to GroundsBot
      
      GroundsBot navigates to each waypoint and waits for ten seconds
      
          Place flag by GroundsBot at each way point
      
      GroundsBot returns home
      
      Set GroundsBot orientation to original home orientation using remote control

  Test:
  
      Power on Groundsbot
      
      Establish connection between GroundsBot and laptop
      
      Send GPS waypoints to GroundsBot
      
      GroundsBot navigates to each waypoint
      
      GroundsBot returns to home position
    
  Criteria:
  
      GroundsBot navigates to each waypoint entered within 2 feet, in the order they were entered

      Once the last waypoint is reached, GroundsBot navigates back to starting position within 2 feet

Test 2:

Test 2 has been designed to demonstrate base functionality of the perception subsystem. The team will present a perception algorithm capable of differentiating between grass (i.e. a mowable surface) and non-grass (i.e. a non-mowable surface.) This test will be performed outside of the fall validation experiment and a replay of the test will be displayed during the fall validation experiment.
  Location: Offline (golf course tbd), report generated for FVE
  
  Equipment: camera, laptop, prototype classification app

  Procedure:
      
      Boot application
      
      Walk to golf course rough, at least 10 feet from fairway boundary
      
      Set app to train on rough
      
      Walk around rough for 10 minutes
      
      Disable training on app
      
      Walk to golf course fairway, at least 10 feet from rough boundary
      
      Set app to train on fairway
      
      Walk around fairway for 10 minutes
      
      Disable training on app
      
      Walk to paved surface
      
      Set app to train on paved surface
      
      Walk around paved surface for 10 minutes
      
      Set app to classification mode
      
      Walk around fairway while app logs classification, gathering at least 50 images
      
      Walk around rough while app logs classifications, gathering at least 50 images
      
      Walk around path while app logs classifications, gathering at least 50 images

  Criteria:
      
      Algorithm classifies rough / fairway with 90% accuracy

      Algorithm classifies grass /paved area with 90% accuracy

Test 3:
  Location: Field by Doherty Apartments

  Equipment: GroundsBot, GroundsBot RTK base station, laptop
  
  Procedure:
  
      GroundsBot directed to move in straight line
  
      GroundBot team member engages emergency stop
 
  Criteria:

      GroundsBot ceases to move within 2 seconds

Spring Validation Experiment

	The spring validation experiment will be when the team will test the full GroundsBot system to demonstrate that all system requirements have been met. The details of the test are laid out below.

Test 1:

  Location: Field by Doherty Apartments

  Equipment: GroundsBot, GroundsBot RTK base station, laptop, Five obstacles (one at minimum of performance requirements)

      Power on GroundsBot

      Open UI on laptop and establish a connection with GroundsBot

      Have a new user use UI to define boundaries of area to be mowed

      Use the UI to submit the mowing area to GroundsBot

      Area shall contain 5 static obstacles, such as trees, bushes, boxes etc..., one of which is minimum size from performance requirements

      GroundsBot will develop a coverage plan of the area input by the user

      GroundsBot mows area per performance requirements

      GroundsBot returns to starting position per performance requirements

Test 2:
  Location: Field by Doherty Apartments

  Equipment: GroundsBot, GroundsBot RTK base station, laptop, soccer ball

  GroundsBot is directed to move in a straight line

  Team throws a soccerball in front of GroundsBot 5 times

  GroundsBot stops until obstacle is out of range per performance requirements

Test 3:
  Location: Field by Doherty Apartments

  Equipment: GroundsBot, GroundsBot RTK base station, laptop

  Test conducted offline, presented at FVE
    
    User enters a mowing boundary containing a slope at maximum performance requirement
    
    GroundsBot successfully mows the region

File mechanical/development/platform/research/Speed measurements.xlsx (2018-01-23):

Time | Distance = 50 ft
11.11
10.9
10.96
10.92
11.03
Average Time:
10.984
Distance in meters:
15.24
Speed:
1.387472688 | meters/sec
3.103693154 | miles/hour
Mowing deck width:
18 | in
0.4572 | meters
With 20% overlap:
0.36576
1 Acre:
4046.86 | meters^2
Time to mow 1 acre:
7974.39105 | seconds
132.9065175 | minutes
2.215108625 | hours
Time to mow 1/8 acre:
0.2768885781 | hours
16.61331469

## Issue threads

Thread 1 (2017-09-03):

assignment 0.1

jphaneuf, 2017-09-03:

jphaneuf, 2017-09-03:
Task 0.1: Fill out the teaming spreadsheet

Due: August 29 by 6:00 p.m.

Purpose: Recruit your teammates and establish project choices

Please use the Google Docs spreadsheet at https://docs.google.com/spreadsheets/d/11t3RQRVVyFr6-utAknRMJUbec5d_qcniqJkwfvrWHD8/edit#gid=1641706985 (Links to an external site.)Links to an external site. to provide the information asked for there:

Your background information (contact info, undergrad major, expertise)
Your current teammates (if any)
Any conflicts you have before or after the regular class time (for lab scheduling of some teams outside this period)
Potential team "mechanical engineers": list Mon-Fri open 2-hour-or-longer slots
Project preferences (top three choices)
Other (e.g. ideas or questions about projects)
Refer to the Google Docs spreadsheet for info that, as it is filled in, should help you find team members and form a team.

Closed 2017-09-03.

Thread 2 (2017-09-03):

assignment 0.2

jphaneuf, 2017-09-03:

jphaneuf, 2017-09-03:
Task 0.2: Form your team, select your project

Due: September 7 by 6 p.m.

Send email (one email per team) to cmumrsdproject@gmail.com and Prof. Apostolopoulos (da1v@andrew.cmu.edu) (and cc to your teammates) with subject line "Team N: Task 0.2" and the following info:

1. Your team letter and the names of your team members.
2. The name of the project you want to do. The project list is on Blackboard under Course Documents-->Project Information.
3. The name/organization/email of your sponsor/mentor point of contact.
4. The specific application you intend to demonstrate your system performing. It is especially important to make this specific for projects that leave this open-ended, which is admittedly many of them.
5. How your project will involve work in each of the three basic areas: mechanism, electronics/sensing, and programming/controls. This is especially important for projects whose initial descriptions lean heavily or exclusively towards only one or two of these areas.

The information you send us in response to the above need not be long - just a few sentences is fine. Based on what you send, we may have questions, and we may need to iterate to reach an acceptable project description. In keeping with the business course timeline, the absolute deadline for project selection will be the following Monday, September 12. However, I expect quick convergence in most cases (by Thursday or Friday). Questions about teaming and projects between now and then are welcome.

jphaneuf, 2017-09-07:
1. Team A: Joe Phaneuf, Henry Chen, Josh Bennett, Adam Driscoll, David Evans
2. Groundsbot
3. Larry Williams, Discovery Robotics, larry.williams@discovery-robotics.com
4. Groundsbot will perform a variety of groundskeeping duties, such as lawn mowing, leaf blowing, and snow removal.
5. Groundsbot will incorporate mechanical design for the chassis, mounting, and accessory integration, a suite of sensors and power electronics for motion, and will require extensive programming for autonomy (mapping, planning etc...)

Closed 2017-09-22.

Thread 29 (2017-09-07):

Conduct highway department interview

davidjevans, 2017-09-07:
Interview at least 1 person from market to understand goals and problems of groundskeeping in market.

In person interview is preferable, but over the phone works too.

jphaneuf, 2017-09-25:
not enough personnel, can't add people, can hire temporary
focus is mainly on roads (paving, drainage, landscaping crew)
most mowing out on contract
spend ~ 1 million
if want more mowing something has to give
not all of the municipalities , there's a misunderstanding of what the responsibilities are
in the burrows only responsible for certain parts, state is responsible
they do herbicide spraying

jphaneuf, 2017-09-25:
comes down to balancing funding
allocated reasonably well
changed the way they did mowing this year, changed contract, partial mowing and then a full mow

jphaneuf, 2017-09-25:
got a lot of complaints from that, was getting overgrown

jphaneuf, 2017-09-25:
why can't we ask workers to pick up trash as well?

jphaneuf, 2017-09-25:
would mow more just for aesthetics

jphaneuf, 2017-09-25:
if you don't mow trees start to grow

jphaneuf, 2017-09-25:
ramps/intersections there are sight distance issues

jphaneuf, 2017-09-25:
doesn't have a lot of equipment, most of it put out to bid

jphaneuf, 2017-09-25:
usually have a month to mow from a bid

jphaneuf, 2017-09-25:
-send email to jason to get contractor names

jphaneuf, 2017-09-25:
contract might say 'within 1 ft of trees' etc..., people go out to check specs

jphaneuf, 2017-09-25:
large tractors with pull behind mower decks

jphaneuf, 2017-09-25:
4-5 man crew on staff put in place in april w/ weedwackers, small tractor w/ mowing deck, go around and hit areas not on contract, large fields, react to complaints

jphaneuf, 2017-09-25:
any kind of job on the road is in a dangerous job, in traffic, mowing , not on slopes where tractor can flip, use weed whacker instead, for the most part less dangerous than patching potholes

jphaneuf, 2017-09-25:
automation: not yet, still low bid w/ contractors, was trying to find some equipment for picking up garbage, some state had some equipment to do that, cheapest most effective way is still people.  mowing is still in that area, not exploring that way.  don't want to limit a contractor's means or methods.  most creative contractors will win bid.  have seen some remote ones, but mostly just using big tractors.

jphaneuf, 2017-09-25:
there's a push / awareness about green space and storm control, reducing impermeable pavement area, the challenge is maintenance of it.  maintenance budget hasn't changed in several years, with this push for green infrastructure, giving water a place to absorb into ground ,  anything penndot can do to help is useful, several storm water retention places which require maintenance.  who's going to do it, where's the money coming from?

jphaneuf, 2017-09-25:
do a lot of beautification permits, folks paying for that and maintaining.  Tend to do just what they need to maintain safety,

jphaneuf, 2017-09-25:
As PennDot increases green infrastructure, where does money come from?

jphaneuf, 2017-09-25:
pittsburgh wet weather, 28 billion project to reduce runoff, FEMA? hasn't affected penndot yet

jphaneuf, 2017-09-25:
south hills developed 1900s no sight at all into retention of storm water

jphaneuf, 2017-09-25:
have to figure out a way to maintain that greenspace

jphaneuf, 2017-09-25:
jason zang: jzang@pa.gov

Closed 2017-11-17.

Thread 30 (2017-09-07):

Conduct golf course interview

davidjevans, 2017-09-07:
Interview at least 1 person from market to understand goals and problems of groundskeeping in market.

In person interview is preferable, but over the phone works too.

jphaneuf, 2017-09-20:
https://docs.google.com/document/d/1CzhLt9k2ENTY46R5RCMXC3hjxlEqVYoYjuye4EzBJpQ/edit

Closed 2017-09-22.

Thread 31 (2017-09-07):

Conduct parks groundskeeping interview

davidjevans, 2017-09-07:
Interview at least 1 person from market to understand goals and problems of groundskeeping in market.

In person interview is preferable, but over the phone works too.

Closed 2017-11-18.

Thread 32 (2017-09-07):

Conduct commercial lawn care interview

davidjevans, 2017-09-07:
Interview at least 1 person from market to understand goals and problems of groundskeeping in market.

In person interview is preferable, but over the phone works too.

Closed 2017-11-17.

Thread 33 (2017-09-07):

Conduct university groundskeeping interview

davidjevans, 2017-09-07:
Interview at least 1 person from market to understand goals and problems of groundskeeping in market.

In person interview is preferable, but over the phone works too.

Closed 2017-11-17.

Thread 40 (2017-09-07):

Conduct Cemetery Groundskeeping Interview

joshuajbennett, 2017-09-07:
Interview at least 1 person from market to understand goals and problems of groundskeeping in market.

In person interview is preferable, but over the phone works too.

Closed 2017-11-18.

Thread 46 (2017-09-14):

Review Discovery's Research Documents

jphaneuf, 2017-09-14:
Discovery has a stack of reference material for this problem.
Will Review in parallel with Grudsbo market research

Closed 2017-09-14.

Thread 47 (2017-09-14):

Review Discovery's market research documentation

jphaneuf, 2017-09-14:
Larry had some documents relevant to use cases.
Will review parallel to Grudsbo market research

jphaneuf, 2017-09-14:
Fatality report (OSHA Sep 2013 - July 2014)
#12 Grounds Maintenance Workers, death by electrocution triming branches near power lines. occassionally falling branches.  Several instances of rolled mowers.

Relevant: Road repair/ highway maintenance/ sign holder fatalities

jphaneuf, 2017-09-14:
15 most dangerous jobs: 160 fatalities for grounds maintenance in 2007

jphaneuf, 2017-09-14:
$14/hr average wage for grounds maintenance

jphaneuf, 2017-09-14:
Larry was perusing synthetic turf maintenance it appears.
These require cleaning (rather than mowing), not as much for automation out there.

jphaneuf, 2017-09-14:
important point:  Synthetic turf is far from maintenance free, and is in some cases more expensive to maintain than natural grass

jphaneuf, 2017-09-14:
synthetic turf maintenance:
Brushing every 6-8 weeks
Aerating 3 times / year
  'To avoid over settling of the infill, it is necessary to aerate your field with rotating tines that are designed dto penetrate and loosen the infill'
raking every 4-6 weeks
sweeping as needed

jphaneuf, 2017-09-14:
example:
A community level Rugby field:
Natural grass: $244,500 to build
Synthetic: $ 1,050,000

These seem really high....

jphaneuf, 2017-09-14:
operating costs:
rugby, community
synthetic: $38,000 / year
natural grass: $32,100 / year

Closed 2017-09-22.

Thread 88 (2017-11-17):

Integration PCB UVLO comparator oscillates

jphaneuf, 2017-11-17:
Fixed during bringup adding 10uF 0603 bypass capacitor at power supply.
Need to add to design files for next rev..

Closed 2018-05-11.

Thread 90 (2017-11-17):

Integration PCB connector to Jetson J21 wrong BOM number

jphaneuf, 2017-11-17:
40 pos connector has 30pos info. Update next rev.

joshuajbennett, 2018-05-11:
Resolved for end of semester.

Closed 2018-05-11.

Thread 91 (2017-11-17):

Integration PCB needs Arduino USB. Mechanical conflict.

jphaneuf, 2017-11-17:
UART from Jetson is fake news, need to use Jetson USB to Arduino.

Fuse holder is in the way. We can wiggle it in, better to move fuse holder next rev.

zhenrychen, 2017-11-17:
Can we use longer pins into the arduino to generate clearance?

joshuajbennett, 2018-05-11:
We fixed all the fake news.

Closed 2018-05-11.

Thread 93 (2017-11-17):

Navigation Stack Not Working

jdriscoll319, 2017-11-17:
Can't get the nav stack to work without sensor data or a map input

joshuajbennett, 2018-05-11:
We got the nav stack working!

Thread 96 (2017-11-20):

Arduino Mega failed on GroundsBot

jphaneuf, 2017-11-20:
Arduino Mega installed on GroundsBot was working, but failed during a reprogramming attempt (Board still mounted and connected to GroundsBot)

Mega wasn't completely bricked, power supplies ok, shows up as usb device, but can't be programmed

Haven't been able to root cause, but things to keep an eye out for:

- Powering Arduino from USB without rest of system powered on may do weird things, i.e. trying to feed other power systems from USB 5V
- We have an inadvertent chassis ground with our mounting. One metal standoff chewed solder mask on arduino and made contact with a ground plane, ends up connected to aluminum backplane, same happens on Jetson, bob's your uncle that's a chassis ground. Not sure this is a problem.

May have been a fluke, but want to keep an eye out

Closed 2018-05-11.

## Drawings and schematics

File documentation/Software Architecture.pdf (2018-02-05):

# GroundsBot Software

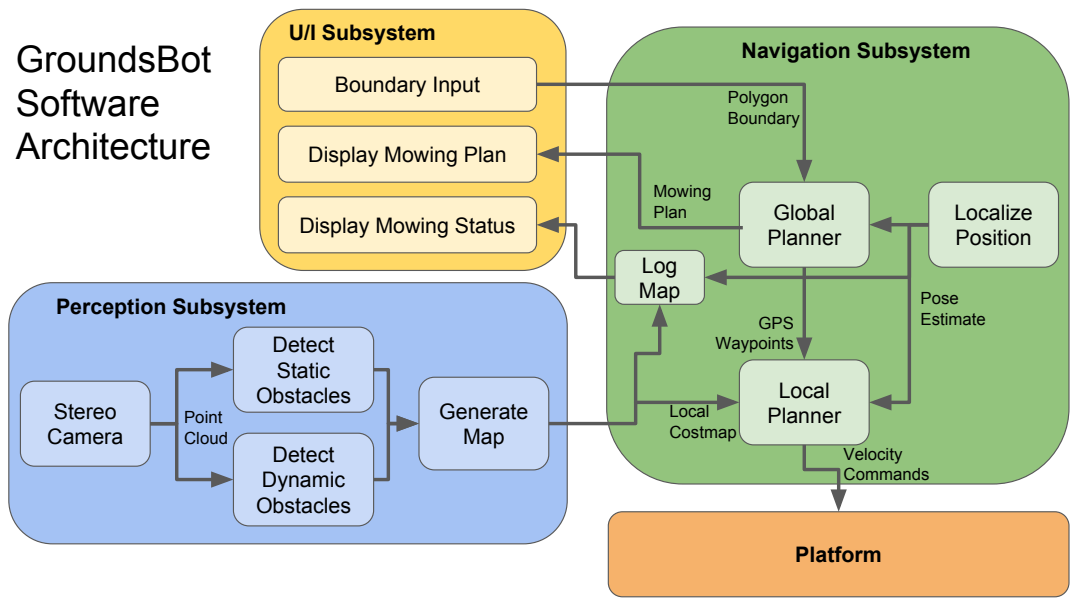
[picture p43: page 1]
Stereo Camera; Detect Static Obstacles; Detect Dynamic Obstacles; Generate Map; Local Planner; Global; Platform; Boundary Input; Localize Position; Polygon Boundary; Velocity Commands; GPS Waypoints; Costmap; Cloud; U/I Subsystem; Perception Subsystem; Navigation Subsystem; Log Map; Architecture

Display Mowing Plan

Mowing Plan

Display Mowing Status

Planner

Pose Estimate

Point

Local

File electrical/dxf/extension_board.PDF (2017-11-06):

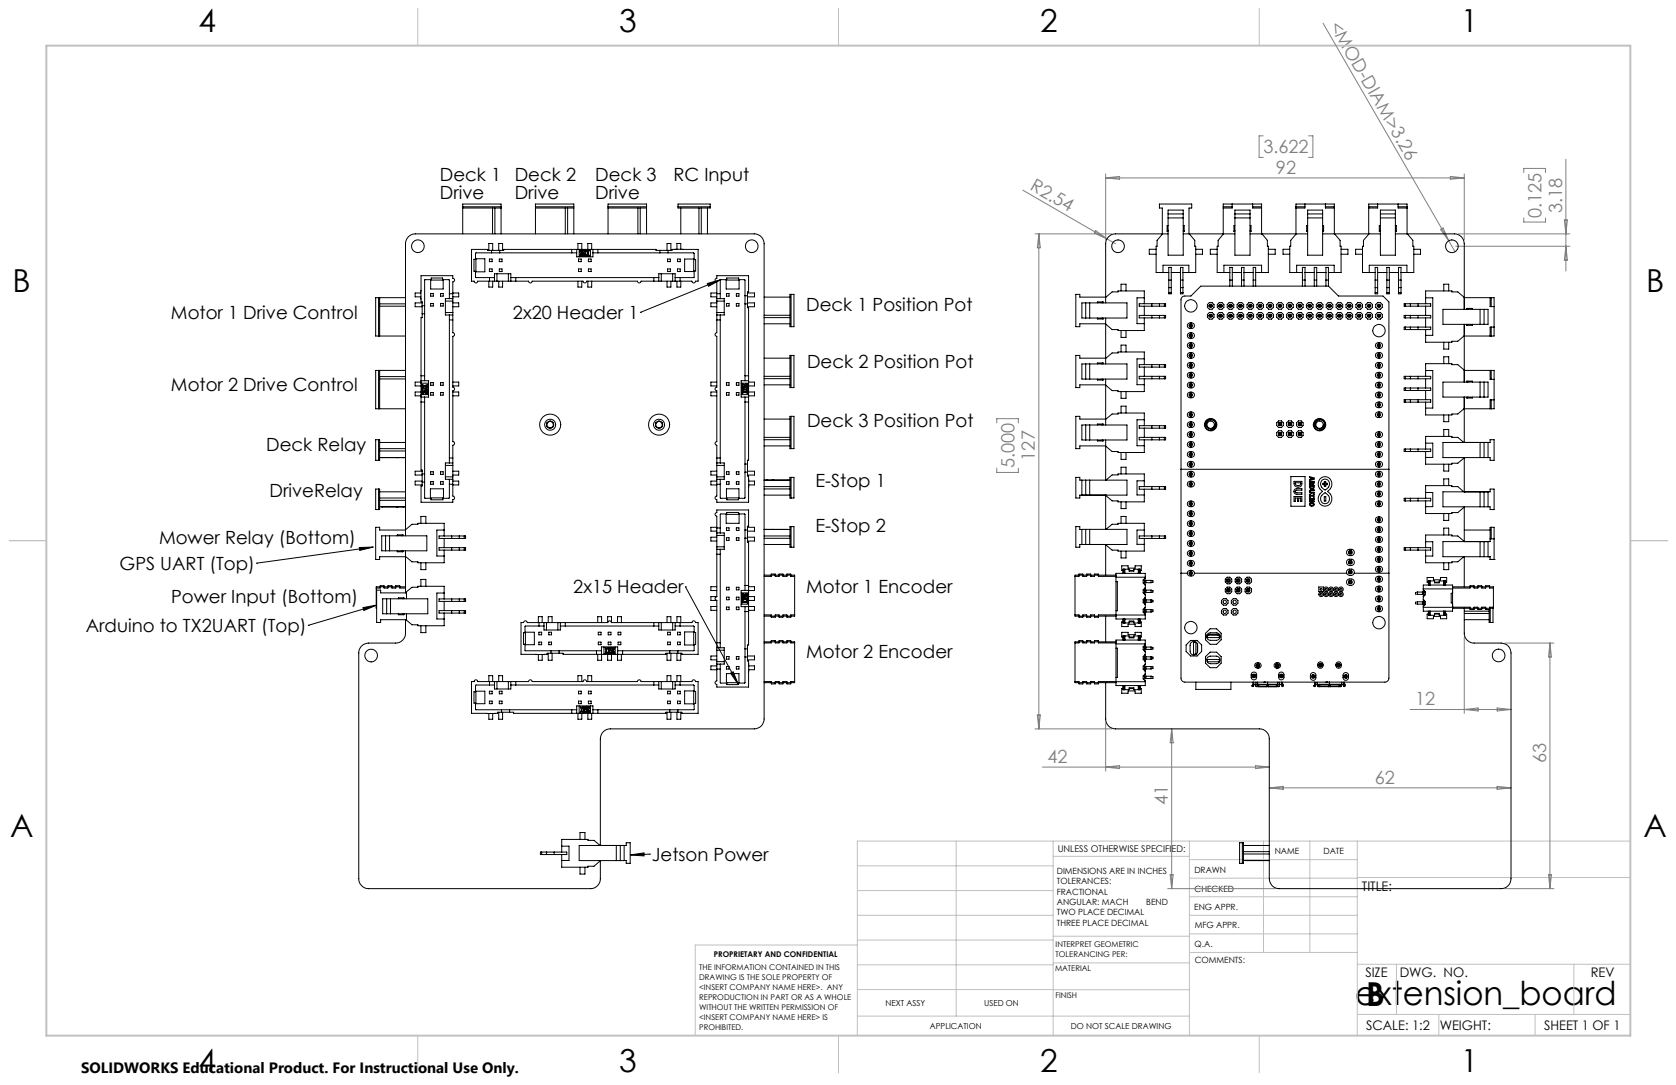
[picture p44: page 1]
Motor 2 Encoder; Motor 1 Encoder; E-Stop 1; E-Stop 2; Deck 2; Deck 1; Jetson Power; 2x20 Header 1; 2x15 Header; Deck Relay

Deck 3 RC Input
Drive

Deck 1 Position Pot

Motor 1 Drive Control

Deck 2 Position Pot

Motor 2 Drive Control

Deck 3 Position Pot

Mower Relay (Bottom)
GPS UART (Top)
Power Input (Bottom)

Arduino to TX2UART (Top)

UNLESS OTHERWISE SPECIFIED: | | NAME | DATE
DIMENSIONS ARE IN INCHES TOLERANCES: FRACTIONAL ANGULAR: MACH BEND TWO PLACE DECIMAL THREE PLACE DECIMAL | DRAWN

CHECKED | | | TITLE:

ENG APPR.
MFG APPR.

INTERPRET GEOMETRIC TOLERANCING PER: | Q.A.
MATERIAL | | SIZE extension_board B | DWG. NO. | REV

PROPRIETARY AND CONFIDENTIAL
THE INFORMATION CONTAINED IN THIS
DRAWING IS THE SOLE PROPERTY OF
<INSERT COMPANY NAME HERE>. ANY
REPRODUCTION IN PART OR AS A WHOLE
WITHOUT THE WRITTEN PERMISSION OF
<INSERT COMPANY NAME HERE> IS
PROHIBITED.

NEXT ASSY | USED ON | FINISH

APPLICATION | DO NOT SCALE DRAWING | | SCALE: 1:2 | WEIGHT: | SHEET 1 OF 1

SOLIDWORKS Educational Product. For Instructional Use Only.

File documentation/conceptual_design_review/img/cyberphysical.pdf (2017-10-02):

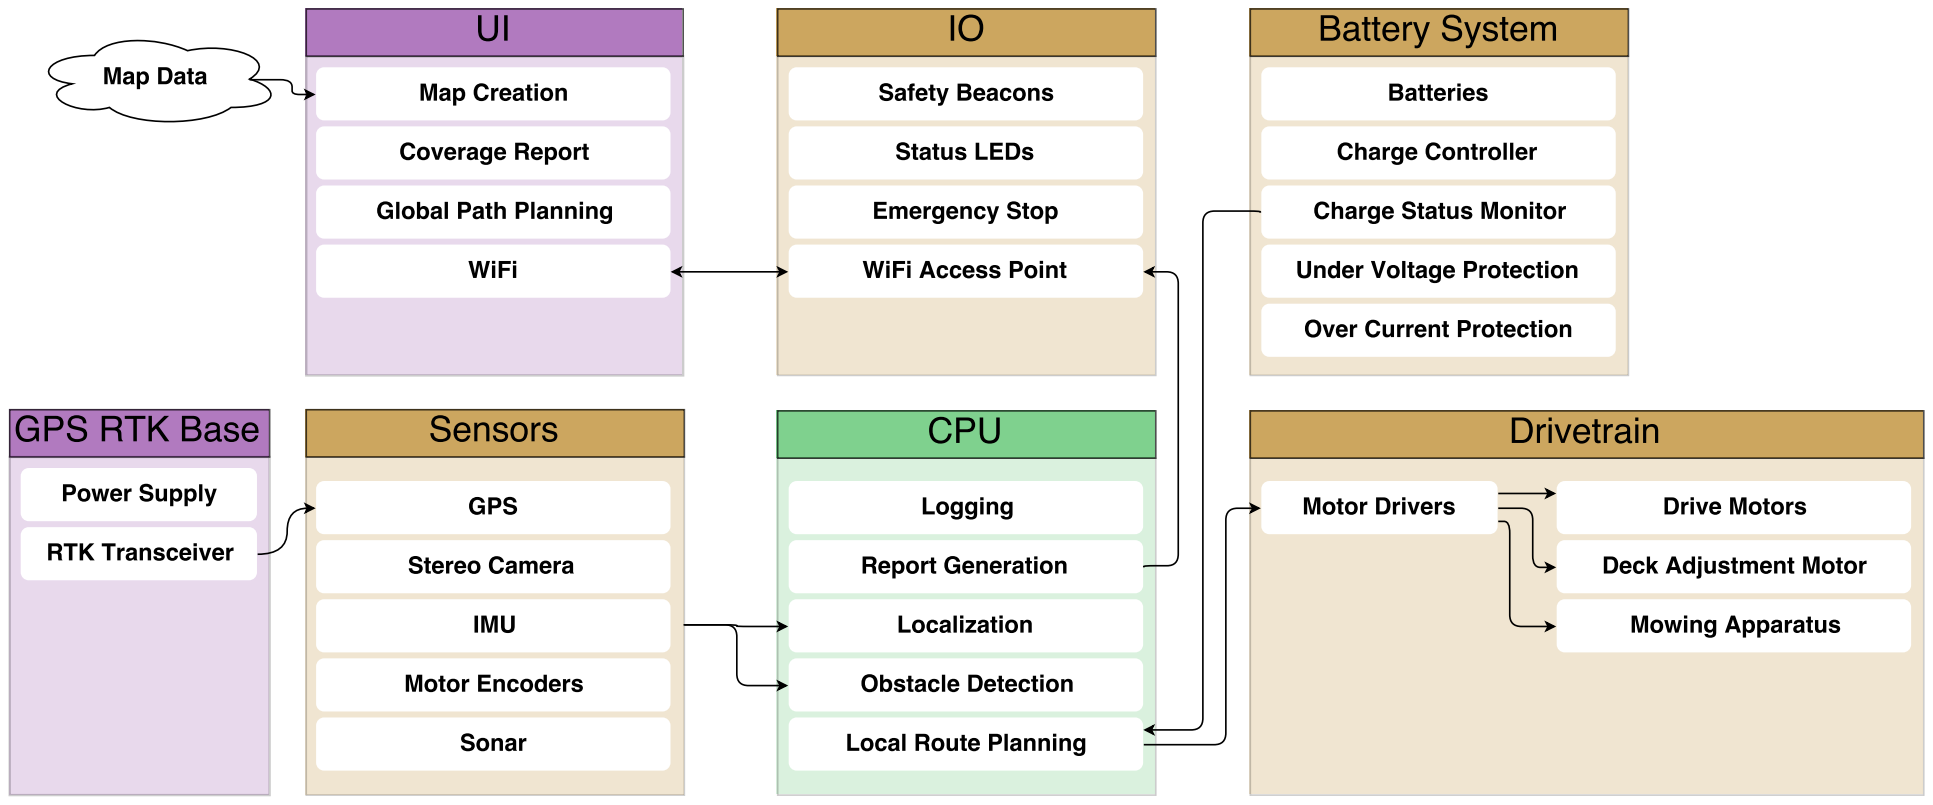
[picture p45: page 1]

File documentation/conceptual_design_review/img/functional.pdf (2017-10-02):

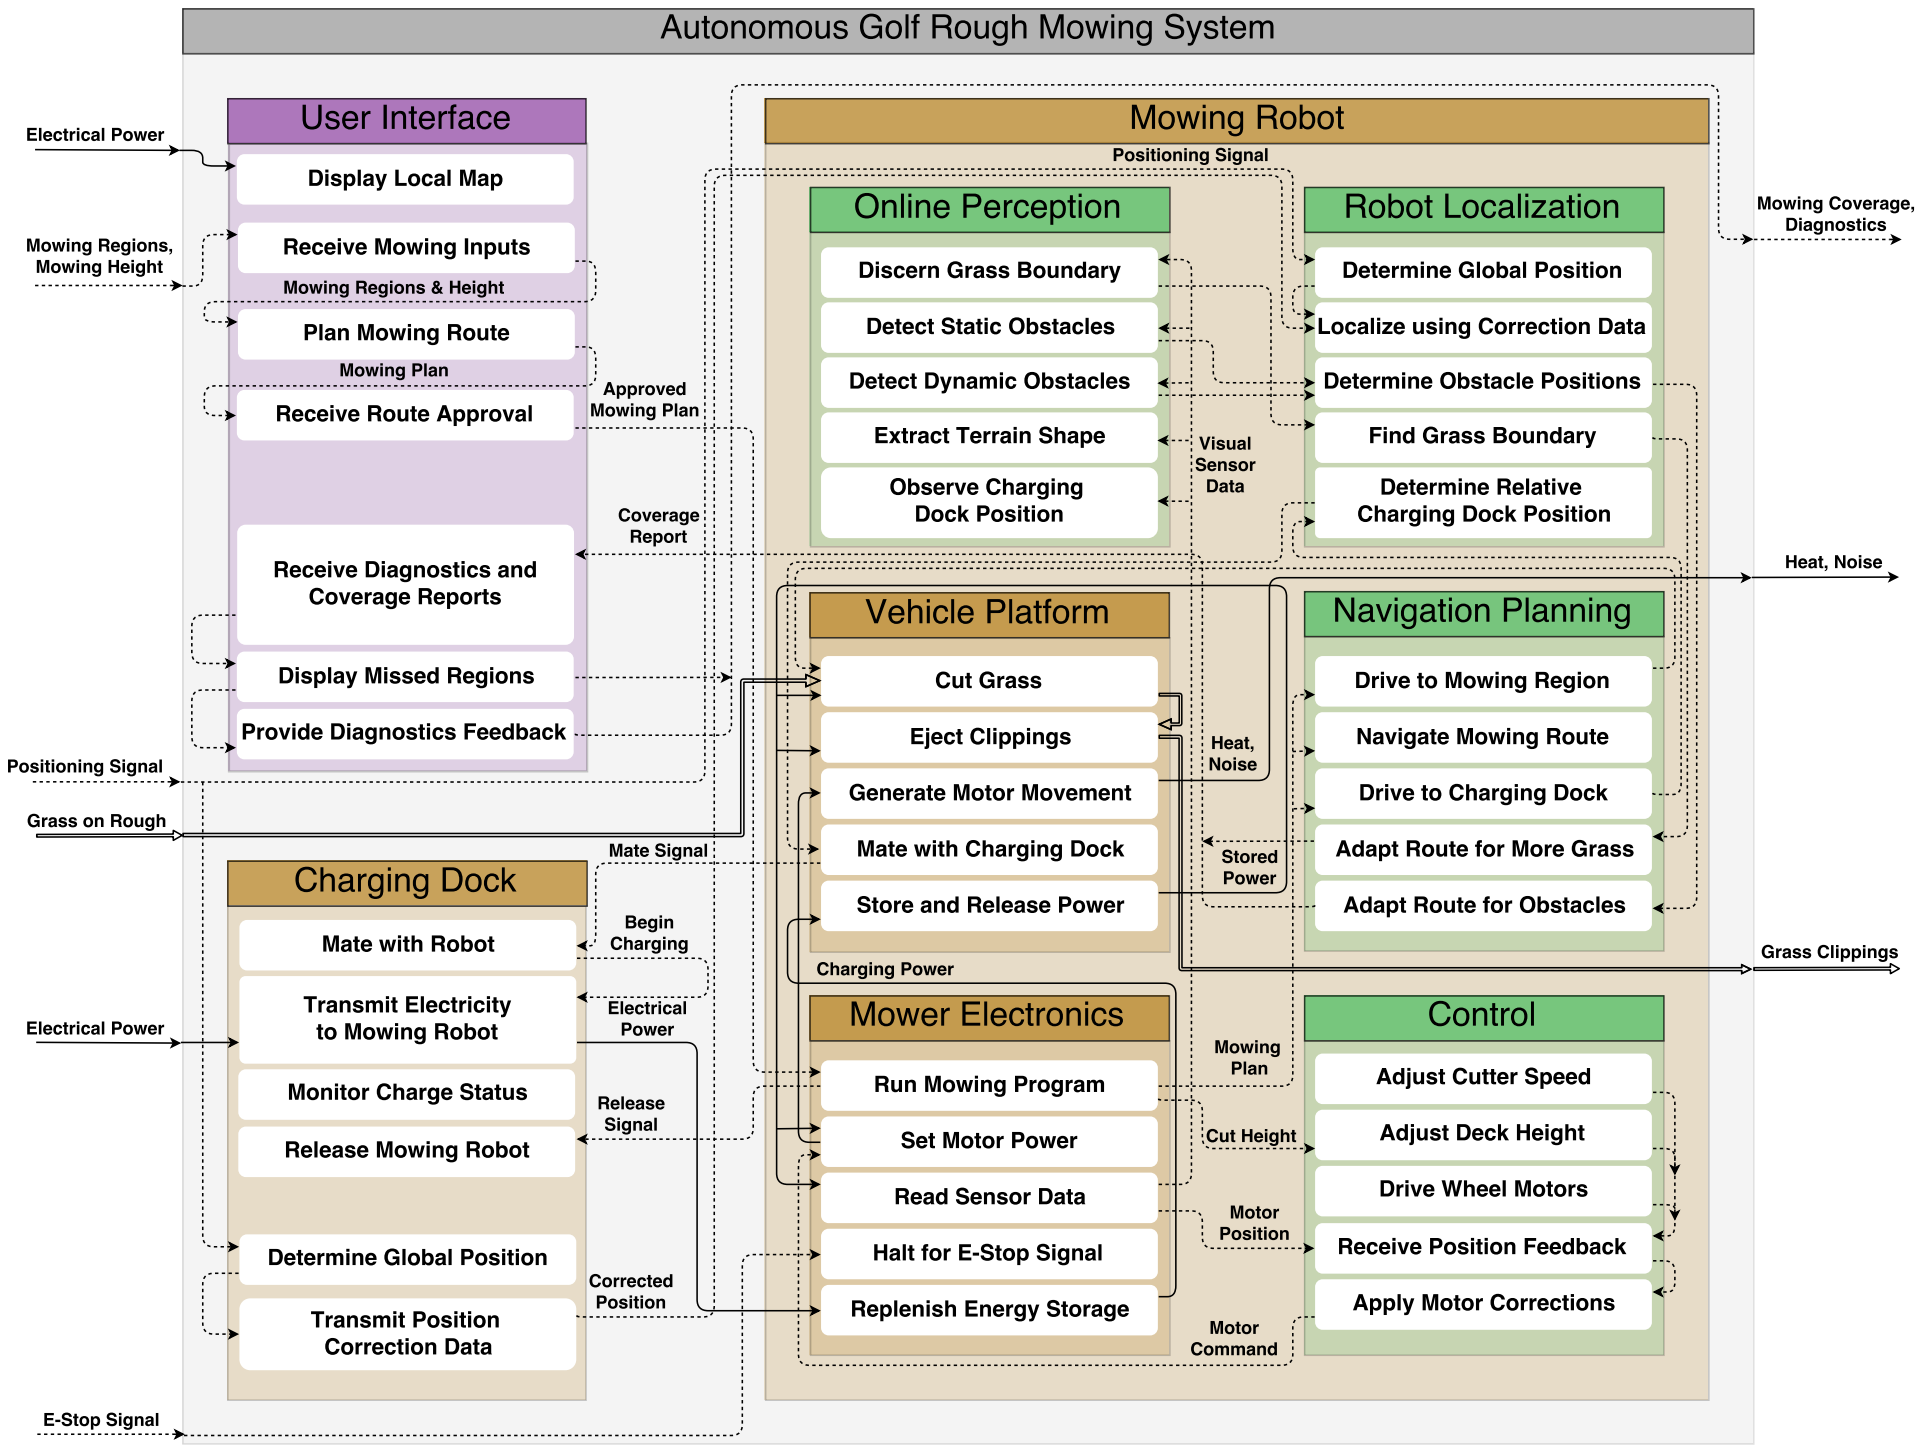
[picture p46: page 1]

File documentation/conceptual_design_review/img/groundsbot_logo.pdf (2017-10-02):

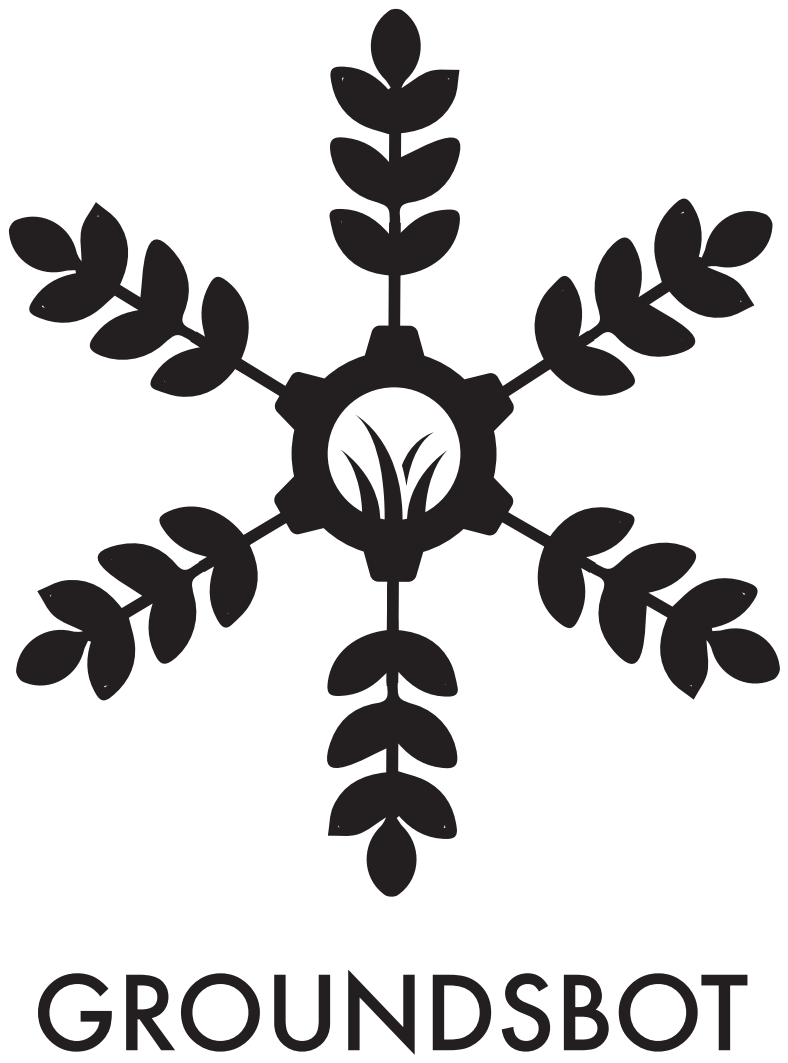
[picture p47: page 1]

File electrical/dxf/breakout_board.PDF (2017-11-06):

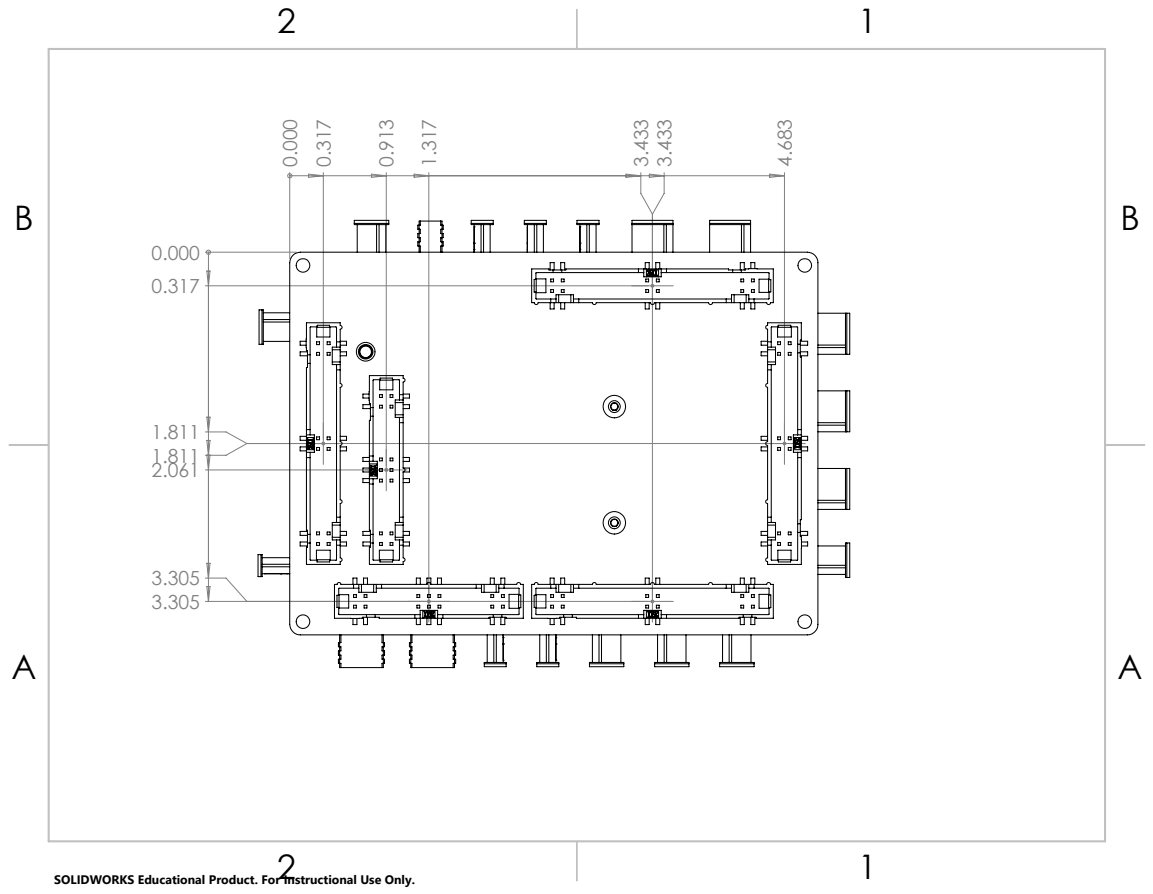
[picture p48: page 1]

SOLIDWORKS Educational Product. For Instructional Use Only.

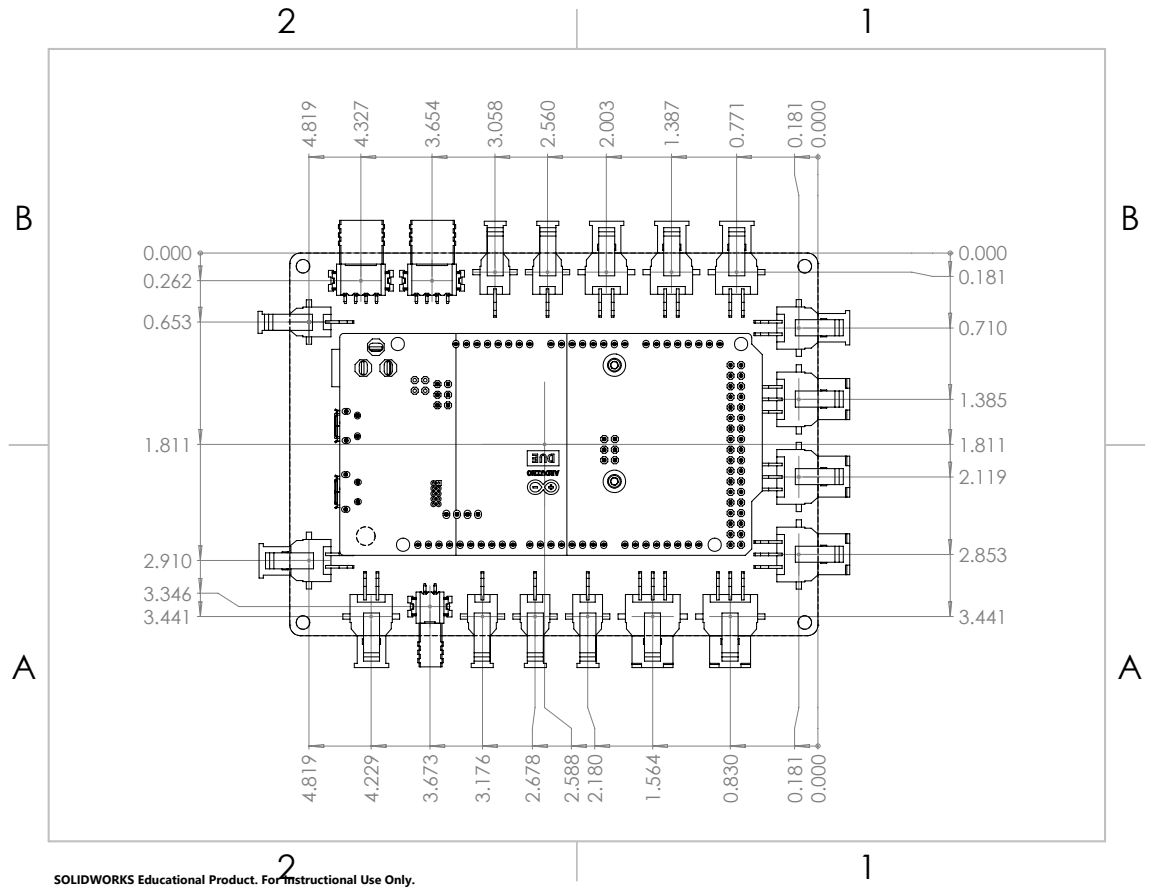
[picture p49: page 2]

SOLIDWORKS Educational Product. For Instructional Use Only.

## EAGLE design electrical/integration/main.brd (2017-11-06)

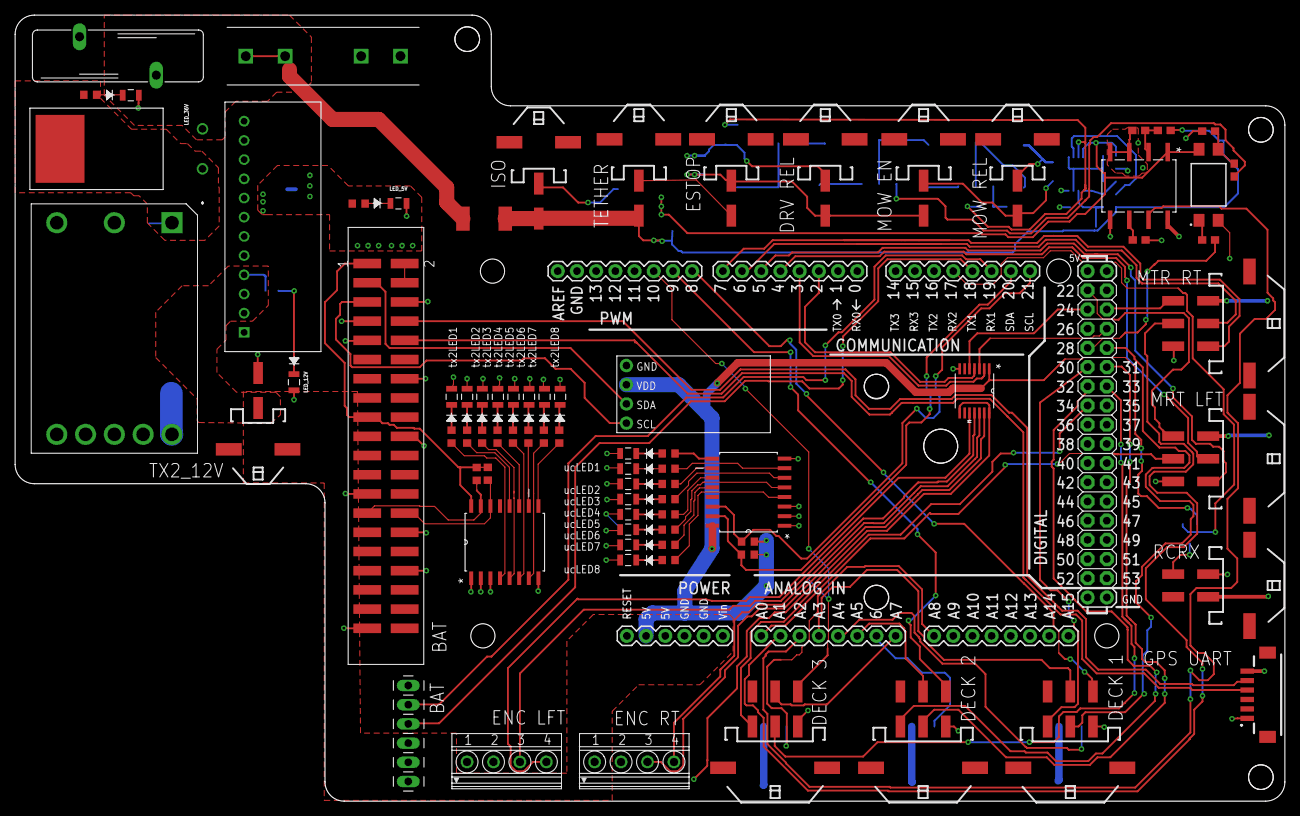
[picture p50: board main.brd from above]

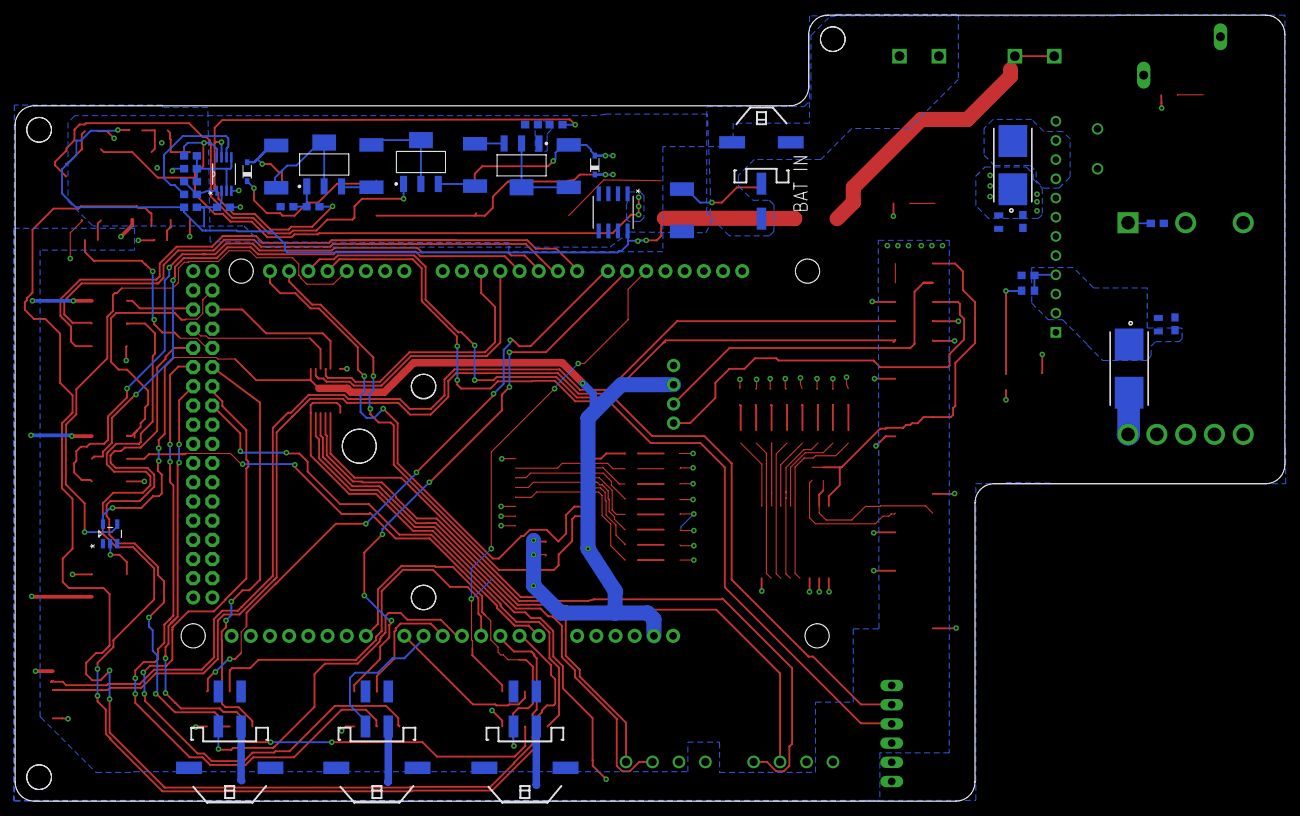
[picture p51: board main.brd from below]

Board: 2 copper layers, 168.0 x 104.0 mm, 114 parts (36 on the bottom side), 116 nets.

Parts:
JETSON1:JETSON_J17_UART1:JP3: 61300611121; 1X06
JETSON1:JETSON_TX2_J21_EXPANSION1:LED1, JETSON1:JETSON_TX2_J21_EXPANSION1:LED2, JETSON1:JETSON_TX2_J21_EXPANSION1:LED3, JETSON1:JETSON_TX2_J21_EXPANSION1:LED4, JETSON1:JETSON_TX2_J21_EXPANSION1:LED5, JETSON1:JETSON_TX2_J21_EXPANSION1:LED6, JETSON1:JETSON_TX2_J21_EXPANSION1:LED7, JETSON1:JETSON_TX2_J21_EXPANSION1:LED8: CMD17-21VGD_TR8; LED_CMD17-21VGD_TR8
JETSON1:JETSON_TX2_J21_EXPANSION1:R1, JETSON1:JETSON_TX2_J21_EXPANSION1:R2, JETSON1:JETSON_TX2_J21_EXPANSION1:R3, JETSON1:JETSON_TX2_J21_EXPANSION1:R4, JETSON1:JETSON_TX2_J21_EXPANSION1:R5, JETSON1:JETSON_TX2_J21_EXPANSION1:R6, JETSON1:JETSON_TX2_J21_EXPANSION1:R7, JETSON1:JETSON_TX2_J21_EXPANSION1:R8: 60; R0603
JETSON1:JETSON_TX2_J21_EXPANSION1:R9, JETSON1:JETSON_TX2_J21_EXPANSION1:R10: 10k; R0603
JETSON1:JETSON_TX2_J21_EXPANSION1:U1: PCF8574ATD; SOIC127P1032X265-16N
JETSON1:JETSON_TX2_J21_EXPANSION1:U$3: TSM-120-XX-XXX-DV; TSM-120-XX-XXX-D
MICROCONTROLLER1:LED1, MICROCONTROLLER1:LED2, MICROCONTROLLER1:LED3, MICROCONTROLLER1:LED4, MICROCONTROLLER1:LED5, MICROCONTROLLER1:LED6, MICROCONTROLLER1:LED7, MICROCONTROLLER1:LED8: CMD17-21VGD_TR8; LED_CMD17-21VGD_TR8
MICROCONTROLLER1:R1, MICROCONTROLLER1:R2, MICROCONTROLLER1:R3, MICROCONTROLLER1:R4, MICROCONTROLLER1:R5, MICROCONTROLLER1:R6, MICROCONTROLLER1:R7, MICROCONTROLLER1:R8: 60; R0603
MICROCONTROLLER1:R9, MICROCONTROLLER1:R10: 10k; R0603
MICROCONTROLLER1:U1: PCF8574ATD; SOIC127P1032X265-16N
MICROCONTROLLER1:U$1: ARDUINO_MEGA_R3FULL; ARDUINO_MEGA
MOTOR_TOP1:JDL, MOTOR_TOP1:JDR, MOTOR_TOP1:X3, MOTOR_TOP1:X4, MOTOR_TOP1:X5: 43045-0609
MOTOR_TOP1:X6, MOTOR_TOP1:X7, MOTOR_TOP1:X8: 43045-0409
POWER_TOP1:C1, POWER_TOP1:C3: 1uF; C0603
POWER_TOP1:C2, POWER_TOP1:C4: 100uF; C0603
POWER_TOP1:F1, POWER_TOP1:F2: 0154004.DR; FUSE_0154004.DR
POWER_TOP1:LED1, POWER_TOP1:LED2, POWER_TOP1:LED3: CMD17-21VGD_TR8; LED_CMD17-21VGD_TR8
POWER_TOP1:MOV1: AVR-M2012C120MT6AB; 0805
POWER_TOP1:MOV2: VC080503A100DP; 0805
POWER_TOP1:R2: 495; R0603
POWER_TOP1:R3: 145; R0603
POWER_TOP1:R4: 1695; R0603
POWER_TOP1:U$1: R-745.0P; SIP-12
POWER_TOP1:U$2: V36SE12004NRFA; V36SE12004NRFA-TH
RC_INPUT1:U1: NC7SZ04M5; SOT95P280X145-5N
RC_INPUT1:X1: 43045-0409
RELAY_CONTROL_TOP1:D2: STPS20M60D; TO220AC
RELAY_CONTROL_TOP1:FH3: FUSE_HOLDER_0.205X0.787IN; LF445_0.807IN
RELAY_CONTROL_TOP1:ISO1:R1, RELAY_CONTROL_TOP1:RELAY_CONTROL1:R11, RELAY_CONTROL_TOP1:RELAY_CONTROL1:R13, RELAY_CONTROL_TOP1:RELAY_CONTROL1:UVLO1:R4: 47k; 0603
RELAY_CONTROL_TOP1:ISO1:R2, RELAY_CONTROL_TOP1:ISO1:R5: 330k; 0603
RELAY_CONTROL_TOP1:ISO1:R3, RELAY_CONTROL_TOP1:ISO1:R4, RELAY_CONTROL_TOP1:RELAY_CONTROL1:R1, RELAY_CONTROL_TOP1:RELAY_CONTROL1:R3: 1.20k; 0603
RELAY_CONTROL_TOP1:ISO1:R6: 2.0k; 0603
RELAY_CONTROL_TOP1:ISO1:U1: AMC1200SDUB; DUB8
RELAY_CONTROL_TOP1:ISO1:U2: SFH615A-3X009T; SOIC254P1016X390-4N
RELAY_CONTROL_TOP1:JBAT, RELAY_CONTROL_TOP1:JDC, RELAY_CONTROL_TOP1:JISO, RELAY_CONTROL_TOP1:JMC, RELAY_CONTROL_TOP1:RELAY_CONTROL1:JESTP, RELAY_CONTROL_TOP1:RELAY_CONTROL1:JMOW, RELAY_CONTROL_TOP1:RELAY_CONTROL1:JTHR: 43045-0209
RELAY_CONTROL_TOP1:MOV1: MOV-20D470K; S20K440
RELAY_CONTROL_TOP1:R1, RELAY_CONTROL_TOP1:R2: RES_0R_2512_1W; R2512
RELAY_CONTROL_TOP1:REGULATOR1:U1: LM2936HVMAX-5.0/NOPB; M08A
RELAY_CONTROL_TOP1:RELAY_CONTROL1:D1, RELAY_CONTROL_TOP1:RELAY_CONTROL1:D2: 1N4148WSTR; SOD323_ST
RELAY_CONTROL_TOP1:RELAY_CONTROL1:RCCB1, RELAY_CONTROL_TOP1:RELAY_CONTROL1:RCCB2, RELAY_CONTROL_TOP1:RELAY_CONTROL1:RCCD, RELAY_CONTROL_TOP1:RELAY_CONTROL1:RCCM: RES_52R3_2512_1W_1%; R2512
RELAY_CONTROL_TOP1:RELAY_CONTROL1:U$2, RELAY_CONTROL_TOP1:RELAY_CONTROL1:U$7, RELAY_CONTROL_TOP1:RELAY_CONTROL1:U$10: ZXTN25100DGTA; SOT230P700X160-4N
RELAY_CONTROL_TOP1:RELAY_CONTROL1:UVLO1:R1: 750K; 0603
RELAY_CONTROL_TOP1:RELAY_CONTROL1:UVLO1:R2: 150k; 0603
RELAY_CONTROL_TOP1:RELAY_CONTROL1:UVLO1:R3: 180k; 0603
RELAY_CONTROL_TOP1:RELAY_CONTROL1:UVLO1:R7: 6.8k; 0603
RELAY_CONTROL_TOP1:RELAY_CONTROL1:UVLO1:R8: 75k; 0603
RELAY_CONTROL_TOP1:RELAY_CONTROL1:UVLO1:U1: LMV762MM; SOP65P490X110-8N
SENSOR_TOP1:ENCODER1:X1, SENSOR_TOP1:ENCODER2:X1: 1751264
SENSOR_TOP1:IMU1:U$1: LSM9DS1; SPARKFUN-9DOF-BREAKOUT
SENSOR_TOP1:REACH_GPS1:U$1: DF13-6P-1.25V; DF13C-6P-1.25V
U301: LSF0204PWR; SOP65P640X120-14N
X101: 43045-0209

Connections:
3V3: MICROCONTROLLER1:R9.2, MICROCONTROLLER1:R10.2, MICROCONTROLLER1:U1.16, MICROCONTROLLER1:U$1.3.3V, RC_INPUT1:U1.5, SENSOR_TOP1:IMU1:U$1.VDD, U301.1
5V: MOTOR_TOP1:JDL.P$1, MOTOR_TOP1:JDR.P$1, MOTOR_TOP1:X6.P$1, MOTOR_TOP1:X7.P$1, MOTOR_TOP1:X8.P$1, POWER_TOP1:C4.1, POWER_TOP1:F1.1, POWER_TOP1:MOV2.1, POWER_TOP1:R3.2, RC_INPUT1:X1.P$2, RELAY_CONTROL_TOP1:ISO1:U1.8, SENSOR_TOP1:ENCODER1:X1.1, SENSOR_TOP1:ENCODER2:X1.1, SENSOR_TOP1:REACH_GPS1:U$1.P$6, U301.8, U301.14
5V_ISO: RELAY_CONTROL_TOP1:ISO1:U1.1, RELAY_CONTROL_TOP1:ISO1:U2.4, RELAY_CONTROL_TOP1:REGULATOR1:U1.1, RELAY_CONTROL_TOP1:RELAY_CONTROL1:UVLO1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.2, RELAY_CONTROL_TOP1:RELAY_CONTROL1:UVLO1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.8
12V: MICROCONTROLLER1:U$1.VIN, POWER_TOP1:C2.1, POWER_TOP1:C3.1, POWER_TOP1:F2.1, POWER_TOP1:MOV1.1, POWER_TOP1:R2.2, POWER_TOP1:U$1.VIN1, POWER_TOP1:U$1.VIN2, POWER_TOP1:U$1.VIN3, X101.P$1
36V: POWER_TOP1:C1.1, POWER_TOP1:R4.2, POWER_TOP1:U$2.+VIN, RELAY_CONTROL_TOP1:D2.1, RELAY_CONTROL_TOP1:D2.2
GND: JETSON1:JETSON_J17_UART1:JP3.1, JETSON1:JETSON_TX2_J21_EXPANSION1:LED1.2, JETSON1:JETSON_TX2_J21_EXPANSION1:LED2.2, JETSON1:JETSON_TX2_J21_EXPANSION1:LED3.2, JETSON1:JETSON_TX2_J21_EXPANSION1:LED4.2, JETSON1:JETSON_TX2_J21_EXPANSION1:LED5.2, JETSON1:JETSON_TX2_J21_EXPANSION1:LED6.2, JETSON1:JETSON_TX2_J21_EXPANSION1:LED7.2, JETSON1:JETSON_TX2_J21_EXPANSION1:LED8.2, JETSON1:JETSON_TX2_J21_EXPANSION1:U1.1, JETSON1:JETSON_TX2_J21_EXPANSION1:U1.2, JETSON1:JETSON_TX2_J21_EXPANSION1:U1.3, JETSON1:JETSON_TX2_J21_EXPANSION1:U1.8, JETSON1:JETSON_TX2_J21_EXPANSION1:U$3.6, JETSON1:JETSON_TX2_J21_EXPANSION1:U$3.9, JETSON1:JETSON_TX2_J21_EXPANSION1:U$3.14, JETSON1:JETSON_TX2_J21_EXPANSION1:U$3.20, JETSON1:JETSON_TX2_J21_EXPANSION1:U$3.25, JETSON1:JETSON_TX2_J21_EXPANSION1:U$3.30, JETSON1:JETSON_TX2_J21_EXPANSION1:U$3.34, JETSON1:JETSON_TX2_J21_EXPANSION1:U$3.39, MICROCONTROLLER1:LED1.2, MICROCONTROLLER1:LED2.2, MICROCONTROLLER1:LED3.2, MICROCONTROLLER1:LED4.2, MICROCONTROLLER1:LED5.2, MICROCONTROLLER1:LED6.2, MICROCONTROLLER1:LED7.2, MICROCONTROLLER1:LED8.2, MICROCONTROLLER1:U1.1, MICROCONTROLLER1:U1.2, MICROCONTROLLER1:U1.3, MICROCONTROLLER1:U1.8, MICROCONTROLLER1:U$1.GND@0, MICROCONTROLLER1:U$1.GND@1, MICROCONTROLLER1:U$1.GND@2, MICROCONTROLLER1:U$1.GND@3, MICROCONTROLLER1:U$1.GND@4, MOTOR_TOP1:JDL.P$6, MOTOR_TOP1:JDR.P$6, MOTOR_TOP1:X3.P$1, MOTOR_TOP1:X4.P$1, MOTOR_TOP1:X5.P$1, MOTOR_TOP1:X6.P$3, MOTOR_TOP1:X7.P$3, MOTOR_TOP1:X8.P$3, POWER_TOP1:C1.2, POWER_TOP1:C2.2, POWER_TOP1:C3.2, POWER_TOP1:C4.2, POWER_TOP1:LED1.2, POWER_TOP1:LED2.2, POWER_TOP1:LED3.2, POWER_TOP1:MOV1.2, POWER_TOP1:MOV2.2, POWER_TOP1:U$1.ENABLE, POWER_TOP1:U$1.GND1, POWER_TOP1:U$1.GND2, POWER_TOP1:U$1.GND3, POWER_TOP1:U$1.GND4, POWER_TOP1:U$2.-VIN, POWER_TOP1:U$2.-VOUT, POWER_TOP1:U$2.ENABLE, RC_INPUT1:U1.3, RC_INPUT1:X1.P$1, RELAY_CONTROL_TOP1:ISO1:R2.1, RELAY_CONTROL_TOP1:ISO1:U1.5, RELAY_CONTROL_TOP1:ISO1:U2.2, RELAY_CONTROL_TOP1:JBAT.P$1, RELAY_CONTROL_TOP1:MOV1.2, RELAY_CONTROL_TOP1:R1.2, SENSOR_TOP1:ENCODER1:X1.2, SENSOR_TOP1:ENCODER2:X1.2, SENSOR_TOP1:IMU1:U$1.GND, SENSOR_TOP1:REACH_GPS1:U$1.P$1, U301.7, X101.P$2
GND_ISO: RELAY_CONTROL_TOP1:ISO1:R1.1, RELAY_CONTROL_TOP1:ISO1:R6.1, RELAY_CONTROL_TOP1:ISO1:U1.3, RELAY_CONTROL_TOP1:ISO1:U1.4, RELAY_CONTROL_TOP1:JISO.P$1, RELAY_CONTROL_TOP1:R1.1, RELAY_CONTROL_TOP1:REGULATOR1:U1.2, RELAY_CONTROL_TOP1:REGULATOR1:U1.3, RELAY_CONTROL_TOP1:REGULATOR1:U1.6, RELAY_CONTROL_TOP1:REGULATOR1:U1.7, RELAY_CONTROL_TOP1:RELAY_CONTROL1:R11.2, RELAY_CONTROL_TOP1:RELAY_CONTROL1:R13.2, RELAY_CONTROL_TOP1:RELAY_CONTROL1:RCCD.1, RELAY_CONTROL_TOP1:RELAY_CONTROL1:U$2.3, RELAY_CONTROL_TOP1:RELAY_CONTROL1:UVLO1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.1, RELAY_CONTROL_TOP1:RELAY_CONTROL1:UVLO1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.1, RELAY_CONTROL_TOP1:RELAY_CONTROL1:UVLO1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.4
JETSON1:JETSON_TX2_J21_EXPANSION1:I2C_GP1_CLK_3V3: JETSON1:JETSON_TX2_J21_EXPANSION1:R10.1, JETSON1:JETSON_TX2_J21_EXPANSION1:U1.14, JETSON1:JETSON_TX2_J21_EXPANSION1:U$3.28
JETSON1:JETSON_TX2_J21_EXPANSION1:I2C_GP1_DAT_3V3: JETSON1:JETSON_TX2_J21_EXPANSION1:R9.1, JETSON1:JETSON_TX2_J21_EXPANSION1:U1.15, JETSON1:JETSON_TX2_J21_EXPANSION1:U$3.27
JETSON1:JETSON_TX2_J21_EXPANSION1:N$1: JETSON1:JETSON_TX2_J21_EXPANSION1:LED8.1, JETSON1:JETSON_TX2_J21_EXPANSION1:R8.1
JETSON1:JETSON_TX2_J21_EXPANSION1:N$2: JETSON1:JETSON_TX2_J21_EXPANSION1:LED7.1, JETSON1:JETSON_TX2_J21_EXPANSION1:R7.1
JETSON1:JETSON_TX2_J21_EXPANSION1:N$3: JETSON1:JETSON_TX2_J21_EXPANSION1:LED6.1, JETSON1:JETSON_TX2_J21_EXPANSION1:R6.1
JETSON1:JETSON_TX2_J21_EXPANSION1:N$4: JETSON1:JETSON_TX2_J21_EXPANSION1:LED5.1, JETSON1:JETSON_TX2_J21_EXPANSION1:R5.1
JETSON1:JETSON_TX2_J21_EXPANSION1:N$5: JETSON1:JETSON_TX2_J21_EXPANSION1:LED4.1, JETSON1:JETSON_TX2_J21_EXPANSION1:R4.1
JETSON1:JETSON_TX2_J21_EXPANSION1:N$6: JETSON1:JETSON_TX2_J21_EXPANSION1:LED3.1, JETSON1:JETSON_TX2_J21_EXPANSION1:R3.1
JETSON1:JETSON_TX2_J21_EXPANSION1:N$7: JETSON1:JETSON_TX2_J21_EXPANSION1:LED2.1, JETSON1:JETSON_TX2_J21_EXPANSION1:R2.1
JETSON1:JETSON_TX2_J21_EXPANSION1:N$8: JETSON1:JETSON_TX2_J21_EXPANSION1:LED1.1, JETSON1:JETSON_TX2_J21_EXPANSION1:R1.1
JETSON1:JETSON_TX2_J21_EXPANSION1:N$9: JETSON1:JETSON_TX2_J21_EXPANSION1:R8.2, JETSON1:JETSON_TX2_J21_EXPANSION1:U1.12
JETSON1:JETSON_TX2_J21_EXPANSION1:N$10: JETSON1:JETSON_TX2_J21_EXPANSION1:R7.2, JETSON1:JETSON_TX2_J21_EXPANSION1:U1.11
JETSON1:JETSON_TX2_J21_EXPANSION1:N$11: JETSON1:JETSON_TX2_J21_EXPANSION1:R6.2, JETSON1:JETSON_TX2_J21_EXPANSION1:U1.10
JETSON1:JETSON_TX2_J21_EXPANSION1:N$12: JETSON1:JETSON_TX2_J21_EXPANSION1:R5.2, JETSON1:JETSON_TX2_J21_EXPANSION1:U1.9
JETSON1:JETSON_TX2_J21_EXPANSION1:N$13: JETSON1:JETSON_TX2_J21_EXPANSION1:R4.2, JETSON1:JETSON_TX2_J21_EXPANSION1:U1.7
JETSON1:JETSON_TX2_J21_EXPANSION1:N$14: JETSON1:JETSON_TX2_J21_EXPANSION1:R3.2, JETSON1:JETSON_TX2_J21_EXPANSION1:U1.6
JETSON1:JETSON_TX2_J21_EXPANSION1:N$15: JETSON1:JETSON_TX2_J21_EXPANSION1:R2.2, JETSON1:JETSON_TX2_J21_EXPANSION1:U1.5
JETSON1:JETSON_TX2_J21_EXPANSION1:N$16: JETSON1:JETSON_TX2_J21_EXPANSION1:R1.2, JETSON1:JETSON_TX2_J21_EXPANSION1:U1.4
JETSON1:JETSON_TX2_J21_EXPANSION1:VDD_3V3_SYS: JETSON1:JETSON_TX2_J21_EXPANSION1:R9.2, JETSON1:JETSON_TX2_J21_EXPANSION1:R10.2, JETSON1:JETSON_TX2_J21_EXPANSION1:U1.16, JETSON1:JETSON_TX2_J21_EXPANSION1:U$3.1, JETSON1:JETSON_TX2_J21_EXPANSION1:U$3.17
JETSON1:JETSON_TX2_J21_EXPANSION1:VDD_5V0_IO_SYS: JETSON1:JETSON_TX2_J21_EXPANSION1:U$3.2, JETSON1:JETSON_TX2_J21_EXPANSION1:U$3.4
MICROCONTROLLER1:LED_SCL: MICROCONTROLLER1:R10.1, MICROCONTROLLER1:U1.14, MICROCONTROLLER1:U$1.21
MICROCONTROLLER1:LED_SDA: MICROCONTROLLER1:R9.1, MICROCONTROLLER1:U1.15, MICROCONTROLLER1:U$1.20
MICROCONTROLLER1:N$1: MICROCONTROLLER1:LED8.1, MICROCONTROLLER1:R8.1
MICROCONTROLLER1:N$2: MICROCONTROLLER1:R1.2, MICROCONTROLLER1:U1.4
MICROCONTROLLER1:N$3: MICROCONTROLLER1:LED7.1, MICROCONTROLLER1:R7.1
MICROCONTROLLER1:N$12: MICROCONTROLLER1:LED6.1, MICROCONTROLLER1:R6.1
MICROCONTROLLER1:N$13: MICROCONTROLLER1:LED5.1, MICROCONTROLLER1:R5.1
MICROCONTROLLER1:N$14: MICROCONTROLLER1:LED4.1, MICROCONTROLLER1:R4.1
MICROCONTROLLER1:N$15: MICROCONTROLLER1:LED3.1, MICROCONTROLLER1:R3.1
MICROCONTROLLER1:N$16: MICROCONTROLLER1:LED2.1, MICROCONTROLLER1:R2.1
MICROCONTROLLER1:N$17: MICROCONTROLLER1:LED1.1, MICROCONTROLLER1:R1.1
MICROCONTROLLER1:N$18: MICROCONTROLLER1:R8.2, MICROCONTROLLER1:U1.12
MICROCONTROLLER1:N$19: MICROCONTROLLER1:R7.2, MICROCONTROLLER1:U1.11
MICROCONTROLLER1:N$20: MICROCONTROLLER1:R6.2, MICROCONTROLLER1:U1.10
MICROCONTROLLER1:N$21: MICROCONTROLLER1:R5.2, MICROCONTROLLER1:U1.9
MICROCONTROLLER1:N$22: MICROCONTROLLER1:R4.2, MICROCONTROLLER1:U1.7
MICROCONTROLLER1:N$23: MICROCONTROLLER1:R3.2, MICROCONTROLLER1:U1.6
MICROCONTROLLER1:N$24: MICROCONTROLLER1:R2.2, MICROCONTROLLER1:U1.5
MOW_EN: MICROCONTROLLER1:U$1.28, RELAY_CONTROL_TOP1:ISO1:R3.2
unnamed: MICROCONTROLLER1:U$1.7, MOTOR_TOP1:JDR.P$3
unnamed: JETSON1:JETSON_TX2_J21_EXPANSION1:U$3.10, SENSOR_TOP1:REACH_GPS1:U$1.P$4
unnamed: MICROCONTROLLER1:U$1.22, MOTOR_TOP1:JDL.P$4
unnamed: MICROCONTROLLER1:U$1.A0, MOTOR_TOP1:JDL.P$5
unnamed: MICROCONTROLLER1:U$1.6, MOTOR_TOP1:JDR.P$2
unnamed: JETSON1:JETSON_TX2_J21_EXPANSION1:U$3.8, SENSOR_TOP1:REACH_GPS1:U$1.P$5
unnamed: MICROCONTROLLER1:U$1.25, MOTOR_TOP1:JDR.P$4
unnamed: MICROCONTROLLER1:U$1.A1, MOTOR_TOP1:JDR.P$5
unnamed: MICROCONTROLLER1:U$1.33, MOTOR_TOP1:X5.P$2
unnamed: MICROCONTROLLER1:U$1.34, MOTOR_TOP1:X5.P$3
unnamed: MICROCONTROLLER1:U$1.10, MOTOR_TOP1:X5.P$4
unnamed: MICROCONTROLLER1:U$1.A8, MOTOR_TOP1:X8.P$2
unnamed: MICROCONTROLLER1:U$1.A7, MOTOR_TOP1:X5.P$5
unnamed: MICROCONTROLLER1:U$1.A6, MOTOR_TOP1:X7.P$2
unnamed: MICROCONTROLLER1:U$1.A5, MOTOR_TOP1:X4.P$5
unnamed: MICROCONTROLLER1:U$1.9, MOTOR_TOP1:X4.P$4
unnamed: MICROCONTROLLER1:U$1.32, MOTOR_TOP1:X4.P$3
unnamed: MICROCONTROLLER1:U$1.31, MOTOR_TOP1:X4.P$2
unnamed: JETSON1:JETSON_TX2_J21_EXPANSION1:U$3.5, SENSOR_TOP1:IMU1:U$1.SCL
unnamed: JETSON1:JETSON_TX2_J21_EXPANSION1:U$3.3, SENSOR_TOP1:IMU1:U$1.SDA
unnamed: MICROCONTROLLER1:U$1.A4, MOTOR_TOP1:X6.P$2
unnamed: MICROCONTROLLER1:U$1.A3, MOTOR_TOP1:X3.P$5
unnamed: MICROCONTROLLER1:U$1.8, MOTOR_TOP1:X3.P$4
unnamed: MICROCONTROLLER1:U$1.30, MOTOR_TOP1:X3.P$3
unnamed: MICROCONTROLLER1:U$1.29, MOTOR_TOP1:X3.P$2
unnamed: MICROCONTROLLER1:U$1.5, MOTOR_TOP1:JDL.P$3
unnamed: MICROCONTROLLER1:U$1.4, MOTOR_TOP1:JDL.P$2
unnamed: JETSON1:JETSON_J17_UART1:JP3.5, MICROCONTROLLER1:U$1.19
unnamed: JETSON1:JETSON_J17_UART1:JP3.4, MICROCONTROLLER1:U$1.18
unnamed: MICROCONTROLLER1:U$1.17, RC_INPUT1:U1.4
unnamed: MICROCONTROLLER1:U$1.2, U301.4
unnamed: MICROCONTROLLER1:U$1.24, U301.5
unnamed: MICROCONTROLLER1:U$1.3, U301.2
unnamed: MICROCONTROLLER1:U$1.27, U301.3
POWER_TOP1:N$1: POWER_TOP1:F2.2, POWER_TOP1:U$2.+VOUT
POWER_TOP1:N$2: POWER_TOP1:F1.2, POWER_TOP1:U$1.VOUT1, POWER_TOP1:U$1.VOUT2, POWER_TOP1:U$1.VOUT3
POWER_TOP1:N$3: POWER_TOP1:LED1.1, POWER_TOP1:R4.1
POWER_TOP1:N$4: POWER_TOP1:LED2.1, POWER_TOP1:R2.1
POWER_TOP1:N$5: POWER_TOP1:LED3.1, POWER_TOP1:R3.1
RC_INPUT1:SBUS_SIG_IN: RC_INPUT1:U1.2, RC_INPUT1:X1.P$3
RELAY_CONTROL_TOP1:36V_RAW: RELAY_CONTROL_TOP1:ISO1:R5.2, RELAY_CONTROL_TOP1:JISO.P$2, RELAY_CONTROL_TOP1:R2.1, RELAY_CONTROL_TOP1:REGULATOR1:U1.8, RELAY_CONTROL_TOP1:RELAY_CONTROL1:JTHR.P$2, RELAY_CONTROL_TOP1:RELAY_CONTROL1:UVLO1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.2
RELAY_CONTROL_TOP1:ISO1:N$1: RELAY_CONTROL_TOP1:ISO1:R2.2, RELAY_CONTROL_TOP1:ISO1:U1.6
RELAY_CONTROL_TOP1:ISO1:N$2: RELAY_CONTROL_TOP1:ISO1:R5.1, RELAY_CONTROL_TOP1:ISO1:R6.2, RELAY_CONTROL_TOP1:ISO1:U1.2
RELAY_CONTROL_TOP1:ISO1:N$3: RELAY_CONTROL_TOP1:ISO1:R1.2, RELAY_CONTROL_TOP1:ISO1:R4.2, RELAY_CONTROL_TOP1:ISO1:U2.3
RELAY_CONTROL_TOP1:ISO1:N$4: RELAY_CONTROL_TOP1:ISO1:R3.1, RELAY_CONTROL_TOP1:ISO1:U2.1
RELAY_CONTROL_TOP1:N$1: RELAY_CONTROL_TOP1:FH3.1, RELAY_CONTROL_TOP1:FH3.2, RELAY_CONTROL_TOP1:JBAT.P$2
RELAY_CONTROL_TOP1:N$2: RELAY_CONTROL_TOP1:JMC.P$2, RELAY_CONTROL_TOP1:RELAY_CONTROL1:D2.C, RELAY_CONTROL_TOP1:RELAY_CONTROL1:JMOW.P$1
RELAY_CONTROL_TOP1:N$3: RELAY_CONTROL_TOP1:JDC.P$2, RELAY_CONTROL_TOP1:RELAY_CONTROL1:D1.C, RELAY_CONTROL_TOP1:RELAY_CONTROL1:JESTP.P$1, RELAY_CONTROL_TOP1:RELAY_CONTROL1:JMOW.P$2
RELAY_CONTROL_TOP1:N$4: RELAY_CONTROL_TOP1:JMC.P$1, RELAY_CONTROL_TOP1:RELAY_CONTROL1:D2.A, RELAY_CONTROL_TOP1:RELAY_CONTROL1:RCCB2.2
RELAY_CONTROL_TOP1:N$5: RELAY_CONTROL_TOP1:ISO1:R4.1, RELAY_CONTROL_TOP1:RELAY_CONTROL1:U$2.1
RELAY_CONTROL_TOP1:N$6: RELAY_CONTROL_TOP1:JDC.P$1, RELAY_CONTROL_TOP1:RELAY_CONTROL1:D1.A, RELAY_CONTROL_TOP1:RELAY_CONTROL1:RCCB1.2
RELAY_CONTROL_TOP1:N$11: RELAY_CONTROL_TOP1:D2.3, RELAY_CONTROL_TOP1:FH3.3, RELAY_CONTROL_TOP1:FH3.4, RELAY_CONTROL_TOP1:MOV1.1, RELAY_CONTROL_TOP1:R2.2
RELAY_CONTROL_TOP1:RELAY_CONTROL1:!UVLO!: RELAY_CONTROL_TOP1:RELAY_CONTROL1:R1.1, RELAY_CONTROL_TOP1:RELAY_CONTROL1:R3.1, RELAY_CONTROL_TOP1:RELAY_CONTROL1:UVLO1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.7
RELAY_CONTROL_TOP1:RELAY_CONTROL1:N$1: RELAY_CONTROL_TOP1:RELAY_CONTROL1:JESTP.P$2, RELAY_CONTROL_TOP1:RELAY_CONTROL1:JTHR.P$1
RELAY_CONTROL_TOP1:RELAY_CONTROL1:N$2: RELAY_CONTROL_TOP1:RELAY_CONTROL1:RCCM.1, RELAY_CONTROL_TOP1:RELAY_CONTROL1:U$2.2, RELAY_CONTROL_TOP1:RELAY_CONTROL1:U$2.4
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

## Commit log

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2017-09-05 Initial mechanical directory structure and platform files.
    [DG-158A-Left Angle.SLDPRT, DG-158A-Right Angle.SLDPRT, E2-X-315-X-D-G-X.SLDPRT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]
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2017-09-29 Updates to tables to make headings bold and lines consistent, inserted groundsbot logo.
    [platform bom.xlsx]
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2017-09-29 Revert "Merge branch 'codr' of https://github.com/MRSD2018/GroundsBot into codr"
    This reverts commit dcff9a1c8da0ec72fd72ce749cf8bbaa237030e0, reversing
    changes made to 340abbacb5c492d5b56f113c05e4860a36fbdd05.
2017-09-29 Revert "Merge branch 'codr' of https://github.com/MRSD2017/GroundsBot into codr"
    This reverts commit 2300cb78b1f64da5ed69180274f07d89a8b673f3, reversing
    changes made to 6f319930390cbd75e13a5aeb5ca7f1524afc1890.
2017-09-29 use case fixed
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2017-09-30 Spring validation change to avoid a part a).
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2017-10-07 Updates to motor calculations and the platform bom.xlsx
    [Motor Calcs.xlsx, platform bom.xlsx]
2017-10-07 Added a model for the motor.
    [Main Frame.SLDPRT]
2017-10-07 Added wheel assemblies, renamed extrusion base, designed wheel mounting.
    [92196A652.SLDPRT, 9684T3.SLDPRT, DG-158A-Left Angle.SLDPRT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]
2017-10-07 Updates to the folder structure: created a research folder for misc files that aren't CAD but related to the platform dev.
    [22925T11.SLDPRT, 22925T17.SLDPRT, Motor Calcs.xlsx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]
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2017-10-07 added other chassis parts
    [Chassis Subassembly.SLDASM, Frame Plate.SLDPRT, Grudsby.SLDASM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]
2017-10-07 added chassis_subassembly to frame_assembly
    [frame_assembly.SLDASM, wheel_assembly.SLDASM]
2017-10-07 Created a top level platform assembly, fixed some issues with the chassis sub assembly
    [22925T17.SLDPRT, 92196A652.SLDPRT, 9684T3.SLDPRT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]
2017-10-07 Refined CAD model for roboteQ brushed motor driver.
    [TE-240-030.SLDPRT]
2017-10-07 updated chassis_assembly to use same sketch
    [chassis_subassembly.SLDASM, frame_assembly.SLDASM, frame_plate.SLDPRT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]
2017-10-07 Changed the assembly hierarchy, fixed weldments and locked down some derived sketches.
    [22925T17.SLDPRT, 92196A652.SLDPRT, 9684T3.SLDPRT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]
2017-10-07 Fixes to the main assembly, added mower blade. Added custom extrusions folder and instructions for how to get solidworks to reference them properly.
    [22925T17.SLDPRT, 92196A652.SLDPRT, 9684T3.SLDPRT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]
2017-10-07 Fixes to the weldments.
    [22925T17.SLDPRT, 92196A652.SLDPRT, 9684T3.SLDPRT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]
2017-10-07 Modifications to extrusion selection.
    [22925T17.SLDPRT, 92196A652.SLDPRT, 9684T3.SLDPRT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]
2017-10-07 Changes to main frame and reconfiguring wheel positions.
    [22925T17.SLDPRT, 92196A652.SLDPRT, 9684T3.SLDPRT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]
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2017-10-07 Created electrical panels and updated weldments with covers and ducts.
    [22925T17.SLDPRT, 91115A403.SLDPRT, 92196A652.SLDPRT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]
2017-10-07 Updates to the frame and integration of electrical panels.
    [22925T17.SLDPRT, 91115A403.SLDPRT, 92196A652.SLDPRT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]
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2017-10-08 Added angle brackets to top extrusion and brackets for caster
    [2444T1.SLDPRT, 47065T153.SLDPRT, 47065T267.SLDPRT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]
2017-10-08 Updates to main frame to add corner extrusions, improved caster brackets. Added mounting hardware for 8020.
    [22925T17.SLDPRT, 22925T17_assy.SLDASM, 22925T17_base.SLDPRT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]
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2017-10-17 Updated frame and did FEA analysis on motor mounts.
    [22925T17_assy.SLDASM, 22925T17_base.SLDPRT, 22925T17_wheel.SLDPRT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]
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2017-10-17 Updated model for mowing platform, continued work on frame. Modelled battery.
    [22925T17_assy.SLDASM, 22925T17_base.SLDPRT, 22925T17_wheel.SLDPRT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]
2017-10-17 Updated mower design to remove plastic battery housing.
    [22925T17_assy.SLDASM, 22925T17_base.SLDPRT, 22925T17_wheel.SLDPRT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]
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2017-10-18 Updated frame with new cross member. LAST COMMIT BEFORE SWITCHING FROM 15 to 10 for extrusions.
    [22925T17_assy.SLDASM, 22925T17_base.SLDPRT, 22925T17_wheel.SLDPRT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]
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2017-10-19 Connecting microcontroller, motor, and sensor module with wires
    [main.sch]
2017-10-19 Microcontroller wires added and RC IN module added
    [main.sch]
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2017-10-19 Finalizing BOM, altering alignment of components. Added stand for Zed camera.
    [22925T17_assy.SLDASM, 22925T17_base.SLDPRT, 22925T17_wheel.SLDPRT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]
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2017-10-22 Add toggle switch library from snapeda
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2017-10-22 add fuses to top bom. Add 25A fuse holder to lib
    [ee_bom_top.csv]
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2017-10-22 add VS-STPS diode for cpu reverse protect, import from digikey
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2017-10-24 add phoenix contact 40A two term modular connector
    [ee_bom_top.csv, main.sch]
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2017-10-24 make stupid diode symbol look like a diode. add power connectors to sch
    [main.sch]
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2017-10-25 spec power for coil drive components. spec uvlo hysteresis.
    [main.sch]
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2017-10-26 replace reed switch with breakout connector
    [main.sch]
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2017-10-28 Hole dimensions and callouts for the electrical panel
    [1704853_00.SLDPRT, 1778780.SLDPRT, 1778858.SLDPRT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]
2017-10-29 added power line and leds in my review
    [main.sch]
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2017-10-30 clean +5V erroneous vdd symbols. clean mismatched nets on DUE breakouts
    [main.sch]
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2017-10-30 add hirose con to Reach gps. swap and relabel uart lines from jetson to reach for clarity
    [main.sch]
2017-10-30 swap ground on motor controller con to align wires
    [main.sch]
2017-10-31 Updates to CAD file for electrical panel and machining.
    [1704853_00.SLDPRT, 1778780.SLDPRT, 1778858.SLDPRT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]
2017-10-31 Switched SBUS on RX0 to SBUS on RX2
    [main.sch]
2017-10-31 Switch SBUS from RX0 to RX2, and connected all arduino grounds
    [main.sch]
2017-10-31 add dxfs and reference mechanical drawings for layout. import connectors positions
    [breakout_board.DXF, breakout_board_bottom_keepout.DXF, breakout_board_top_keepout.DXF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]
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2017-11-01 Updates to the mechanical inputs for the PCB.
    [1704853_00.SLDPRT, 1778780.SLDPRT, 1778858.SLDPRT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]
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2017-11-01 remove motor driver isolation, need the space in layout. will have to add an adapter if necessary later
    [main.sch]
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2017-11-01 replace mow enable toggle with connector. position connectors more
    [main.brd, main.sch]
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2017-11-01 swap coil drive connector polarity for consistency with other connectors
    [main.brd, main.sch]
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2017-11-01 add missing npn base resistor mow en
    [main.brd, main.sch]
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2017-11-02 Redesigned electrical panel for new changes to the PCB design.
    [1704853_00.SLDPRT, 1778780.SLDPRT, 1778858.SLDPRT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]
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2017-11-02 clear width errors
    [main.brd]
2017-11-02 clear top bot clearance issues
    [main.brd, main.sch]
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2017-11-03 fix broken motor schematic links, ipso facto added to PCB
    [main.brd, main.sch]
2017-11-03 Progress on redesigning electrical panel for additional relays.
    [1704853_00.SLDPRT, 1778780.SLDPRT, 1778858.SLDPRT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]
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2017-11-05 update libraries for schematic and pcb for synced bom parameters
    [main.brd, main.sch]
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2017-11-07 Finalizing drawings for electrical panel production, PCIE bracket design revision and new drawing.
    [1751264_04.SLDPRT, 22925T17_assy.SLDASM, 22925T17_base.SLDPRT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]
2017-11-07 init BOM. add resistors to lib with bom parameters
    [groundsbot_bom.csv]
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2017-11-07 replace caps
    [main.sch]
2017-11-07 replace fuse
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2017-11-16 Added a roll cage and adjusted the wheel positions.
    [Rollover Cage.SLDPRT, frame_assembly.SLDASM]
2017-11-22 Changed roll cage per actual positioning and height.
    [Rollover Cage.SLDPRT]
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2017-12-05 Added missing fastener.
    [91075A107.SLDPRT]

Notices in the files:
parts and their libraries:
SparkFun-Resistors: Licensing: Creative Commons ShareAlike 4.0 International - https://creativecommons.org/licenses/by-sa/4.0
